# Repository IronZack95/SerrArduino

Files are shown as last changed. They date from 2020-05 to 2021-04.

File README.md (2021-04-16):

# SerrArduino
> Sistema di Automazione per Serra con Arduino

**Author**
- [IronZack95](https://github.com/IronZack95)
 
 ## Instructions:
 1. A_Global_rev7 contiene il codice che ho scritto per Arduino IDE
 2. per vedere lo schema elettrico aprire "Arduino_Serra.fzz" con FRITZING
 3. Cartella "Test" per testare il funzionamento componenti singoli
 4. Board_Schematic contiene lo schema SPice e un pdf per il pinout della boad millefori

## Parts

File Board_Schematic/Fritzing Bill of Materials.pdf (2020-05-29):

29/5/2020 | Fritzing Bill of Materials
file:///C:/Users/Utente/Documents/GitHub/SerrArduino/Board_Schematic/Arduino_Serra_bom.html | 1/3

# Bill of Materials: Arduino_Serra.fzz

C:/Users/Utente/Documents/GitHub/SerrArduino/Arduino_Serra.fzz
venerdì, maggio 29 2020, 17:27:59

# Assembly List

Label | Part Type | Properties
Componente1 | Arduino Uno
| (Rev3) | tipo Arduino UNO (Rev3)

### DHT11

### DHT11 Humitidy and Temperature Sensor

### ENCODER1

### Rotary Encoder with switch (KY-

040)

variant KY-040; part number KY-040

J1 | Basic Servo
LCD1 | LCD screen | tipo Character; pins 16
M1 | DC Motor

### Modulo

Motore | L293D | package THT; variant L293D

### Part1

KY-022

### Infrared Receiver Module

operating voltage 2.7V to 5.5V; variant variant 1; operating current 0.4 ~ 1.5 mA; low level voltage 0.4V; reception distance 18m; high level voltage 4.5V; ambient light filter up to 500LUX; pin spacing 300mil; dimensions 18.5mm x 15mm [0.728in x 0.591in]; editable pin labels false; reception angle ±45º; operating temperature -25°C to 80°C [-13°F to 176°F]; ir receiver 1838; chip label KY-022; package Breakout board; pins 3

R1 | PHOTOCELL | package photocell-kit; variant pth-kit
R2 | Trimmer

### Potentiometer

| | package THT; size Trimmer - 12mm; track Linear; tipo Trimmer Potentiometer;
| | maximum resistance 10kΩ
R3 | 1k Ω Resistor | package THT; tolerance ±5%; bands 4; resistenza 1kΩ; pin spacing 400 mil

R4

### Temperature Sensor (Thermistor)

| | resistance at 25° 10kΩ; package THT; thermistor type NTC; tipo thermistor
R5 | 10k Ω
| Resistor | package THT; tolerance ±5%; bands 4; resistenza 10kΩ; pin spacing 400 mil
R7 | 500 Ω
| Resistor | package THT; tolerance ±5%; bands 4; resistenza 500Ω; pin spacing 400 mil

file:///C:/Users/Utente/Documents/GitHub/SerrArduino/Board_Schematic/Arduino_Serra_bom.html | 2/3
Label | Part Type | Properties
R9 | 500 Ω
Resistor | package THT; tolerance ±5%; bands 4; resistenza 500Ω; pin spacing 400 mil
Relè | KY-019 5V

### Relay Module

package Breakout board; dimensions 27mm x 34mm [1.063in x 1.338in]; maximum ac 10A 250VAC; operating voltage 5V ~ 12V; editable pin labels false; chip label KY-019; variant variant 1; pins 3; pin spacing 300mil; maximum dc 10A 30VDC
RTC Clock | Adafruit
DS3231 | variant variant 2; part number Adafruit #3013
S1 | Toggle Switch | package THT; switching circuit SPDT
S2 | Toggle Switch | package THT; switching circuit SPDT

# Shopping List

Amount | Part Type | Properties

1

### Arduino Uno

(Rev3) | tipo Arduino UNO (Rev3)

1

### DHT11 Humitidy and Temperature Sensor

1

### Rotary Encoder with switch (KY-

040)

variant KY-040; part number KY-040

1 | Basic Servo
1 | LCD screen | tipo Character; pins 16
1 | DC Motor
1 | L293D | package THT; variant L293D

1

KY-022

### Infrared Receiver Module

operating voltage 2.7V to 5.5V; variant variant 1; operating current 0.4 ~ 1.5 mA; low level voltage 0.4V; reception distance 18m; high level voltage 4.5V; ambient light filter up to 500LUX; pin spacing 300mil; dimensions 18.5mm x 15mm [0.728in x 0.591in]; editable pin labels false; reception angle ±45º; operating temperature -25°C to 80°C [-13°F to 176°F]; ir receiver 1838; chip label KY-022; package Breakout board; pins 3

1 | PHOTOCELL | package photocell-kit; variant pth-kit

1

### Trimmer Potentiometer

| | package THT; size Trimmer - 12mm; track Linear; tipo Trimmer Potentiometer; maximum resistance 10kΩ
1 | 1k Ω Resistor | package THT; tolerance ±5%; bands 4; resistenza 1kΩ; pin spacing 400 mil

1

### Temperature Sensor (Thermistor)

| | resistance at 25° 10kΩ; package THT; thermistor type NTC; tipo thermistor

file:///C:/Users/Utente/Documents/GitHub/SerrArduino/Board_Schematic/Arduino_Serra_bom.html | 3/3
Amount | Part Type | Properties
1 | 10k Ω
| Resistor | package THT; tolerance ±5%; bands 4; resistenza 10kΩ; pin spacing 400 mil
2 | 500 Ω
| Resistor | package THT; tolerance ±5%; bands 4; resistenza 500Ω; pin spacing 400 mil
1 | KY-019 5V
| Relay Module | package Breakout board; dimensions 27mm x 34mm [1.063in x 1.338in]; maximum ac
| | 10A 250VAC; operating voltage 5V ~ 12V; editable pin labels false; chip label KY-019;
| | variant variant 1; pins 3; pin spacing 300mil; maximum dc 10A 30VDC
1 | Adafruit
| DS3231 | variant variant 2; part number Adafruit #3013
2 | Toggle Switch | package THT; switching circuit SPDT

Exported with Fritzing 0.8.7- http://fritzing.org

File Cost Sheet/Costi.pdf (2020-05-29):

Foglio1

29/05/20

TABELLA COSTI
Componente | Prezzo | QTA | Prezzo Totale

GBC ELETTRONICA

Fotoresistenza | 1,2 | 2 | 2,4
Mille Fori | 5 | 1 | 5
| 5 | 1 | 5
L293D Integrato | 5,5 | 1 | 5,5
10k ohm Potenziometro | 1,5 | 1 | 1,5
Stagno 60/40 | 8 | 0,25 | 2
| 0,4 | 2 | 0,8
| 0,8 | 1 | 0,8
Alimentatore 220AC/12DC | 7,9 | 1 | 7,9
Connettore Dorato 40PM | 0,8 | 2 | 1,6
Cavo Alimentazione bianco | 1 | 2 | 2
Spina 220V 10A Bianca | 1,5 | 1 | 1,5
Deviatore 2 vie | 1,5 | 1 | 1,5
Ventola 12V | 4,5 | 1 | 4,5

AMAZON

LERWAY Tappetino Riscaldante | 19,9 | 1 | 19,9
IZOKEE 60 Pezzi Morsetti | 9,9 | 0,5 | 4,95
ELEGOO UNO Rev3 | 12,99 | 1 | 12,99
| 54,99 | 1 | 54,99
| 7,99 | 0,2 | 1,598
| 7 | 0,5 | 3,5
| | | SOMMA
| | | 139,928

## SerrArduino

Modulo Step-Down DC\DC

Piattina Red-Black
Zoccolo16 Pin

ELEGOO Starter Kit
Arceli 5pz
Modulo Irreciver 2pz

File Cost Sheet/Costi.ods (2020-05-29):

SerrArduino | 29/05/20
TABELLA COSTI
Componente | Prezzo | QTA | Prezzo Totale
GBC ELETTRONICA
Fotoresistenza | 1,2 | 2 | 2,4
Mille Fori | 5 | 1 | 5
Modulo Step-Down DC\DC | 5 | 1 | 5
L293D Integrato | 5,5 | 1 | 5,5
10k ohm Potenziometro | 1,5 | 1 | 1,5
Stagno 60/40 | 8 | 0,25 | 2
Piattina Red-Black | 0,4 | 2 | 0,8
Zoccolo16 Pin | 0,8 | 1 | 0,8
Alimentatore 220AC/12DC | 7,9 | 1 | 7,9
Connettore Dorato 40PM | 0,8 | 2 | 1,6
Cavo Alimentazione bianco | 1 | 2 | 2
Spina 220V 10A Bianca | 1,5 | 1 | 1,5
Deviatore 2 vie | 1,5 | 1 | 1,5
Ventola 12V | 4,5 | 1 | 4,5
AMAZON
LERWAY Tappetino Riscaldante | 19,9 | 1 | 19,9
IZOKEE 60 Pezzi Morsetti | 9,9 | 0,5 | 4,95
ELEGOO UNO Rev3 | 12,99 | 1 | 12,99
ELEGOO Starter Kit | 54,99 | 1 | 54,99
Arceli 5pz | 7,99 | 0,2 | 1,598
Modulo Irreciver 2pz | 7 | 0,5 | 3,5
 |  |  | SOMMA
 |  |  | 139,928

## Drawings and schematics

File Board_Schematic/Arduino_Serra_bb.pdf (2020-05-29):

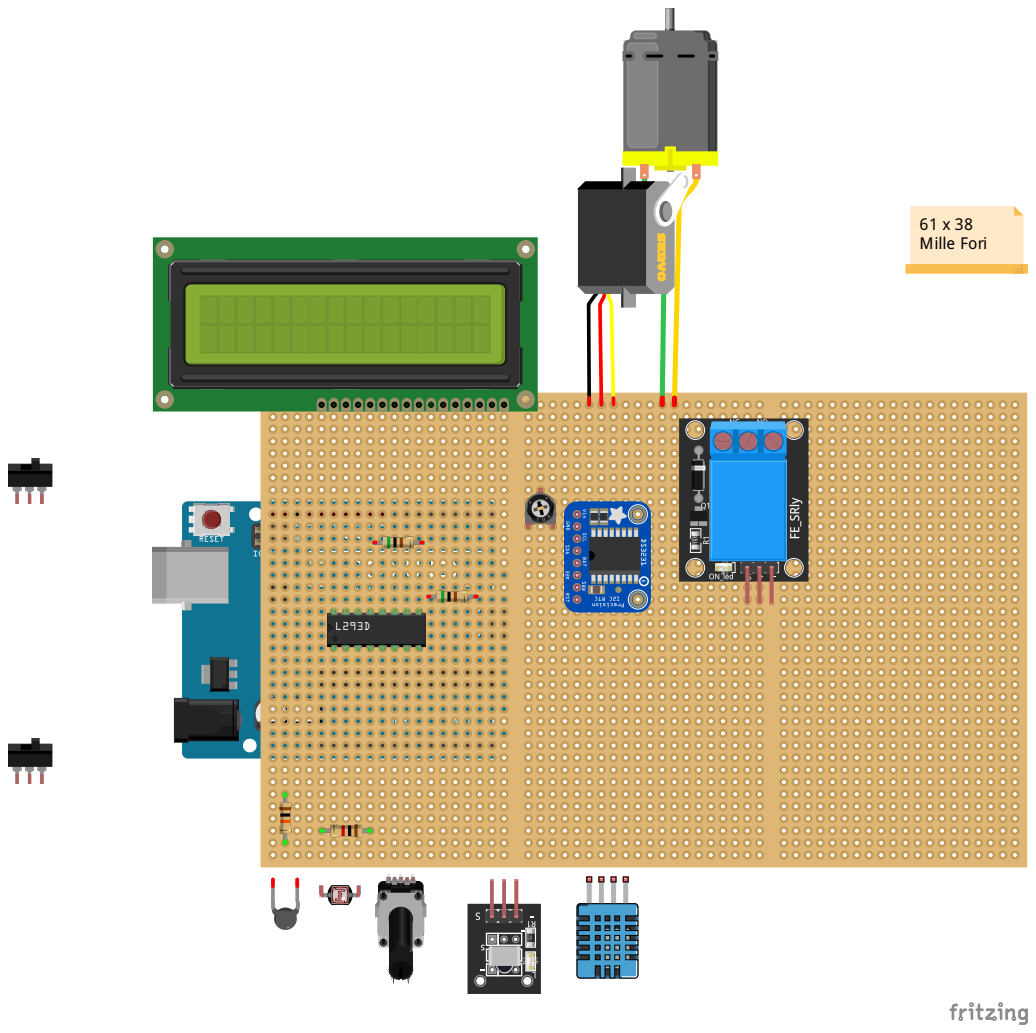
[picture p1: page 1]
61 x 38 Mille Fori

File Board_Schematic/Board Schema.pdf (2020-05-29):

1

2

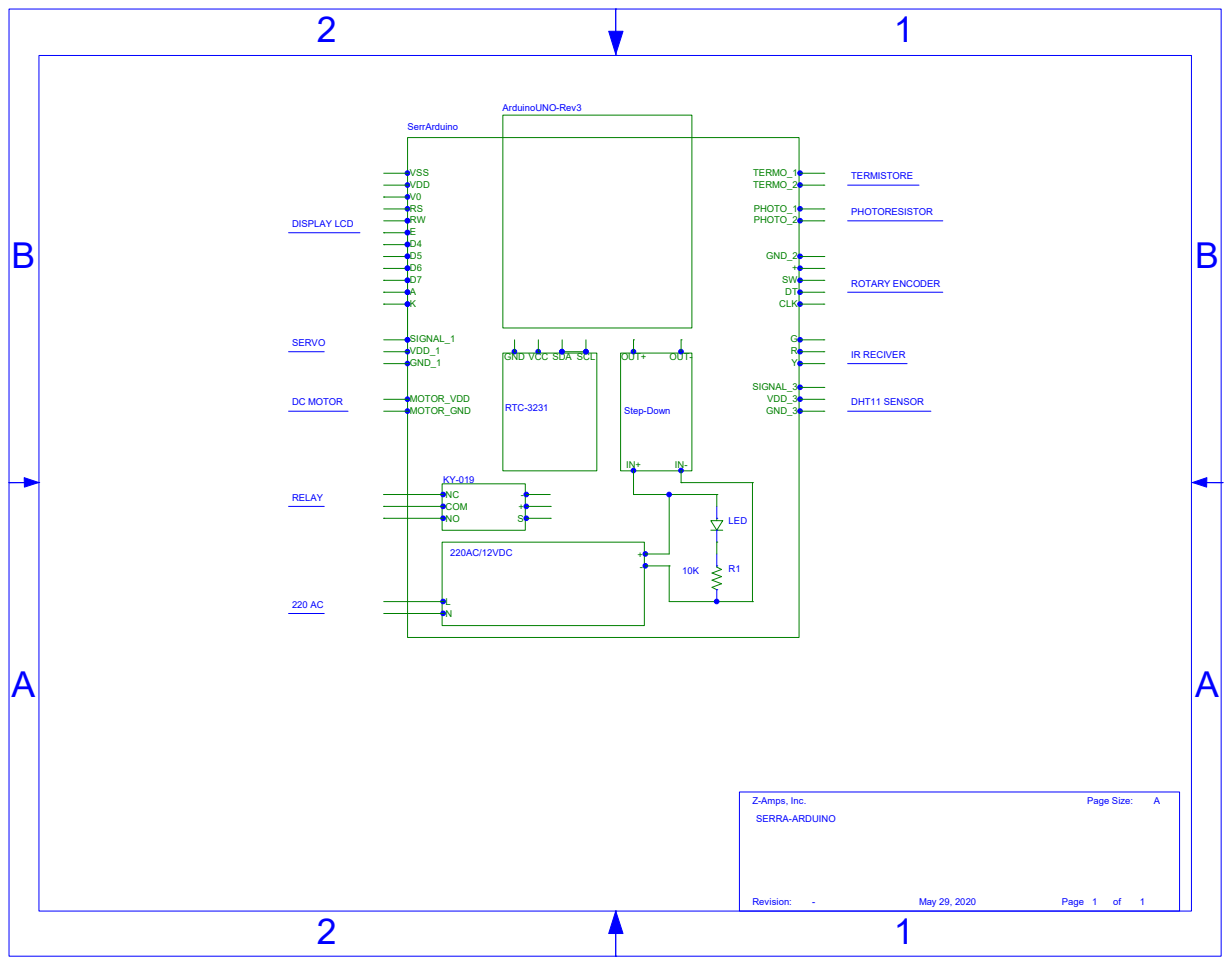
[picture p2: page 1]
COM; 220AC/12VDC; OUT+; OUT-; Step-Down; VSS VDD V0; SIGNAL_1 VDD_1 GND_1; MOTOR_VDD MOTOR_GND; TERMO_1 TERMO_2; PHOTO_1 PHOTO_2; GND_2 + SW DT CLK; SIGNAL_3 VDD_3 GND_3; SerrArduino; LED; ArduinoUNO-Rev3; RTC-3231; Revision:; Page; Z-Amps, Inc.; Page Size:; May 29, 2020; SERVO; DC MOTOR; RELAY; DISPLAY LCD; TERMISTORE; PHOTORESISTOR; IR RECIVER; DHT11 SENSOR; ROTARY ENCODER; SERRA-ARDUINO

GND VCC SDA SCL

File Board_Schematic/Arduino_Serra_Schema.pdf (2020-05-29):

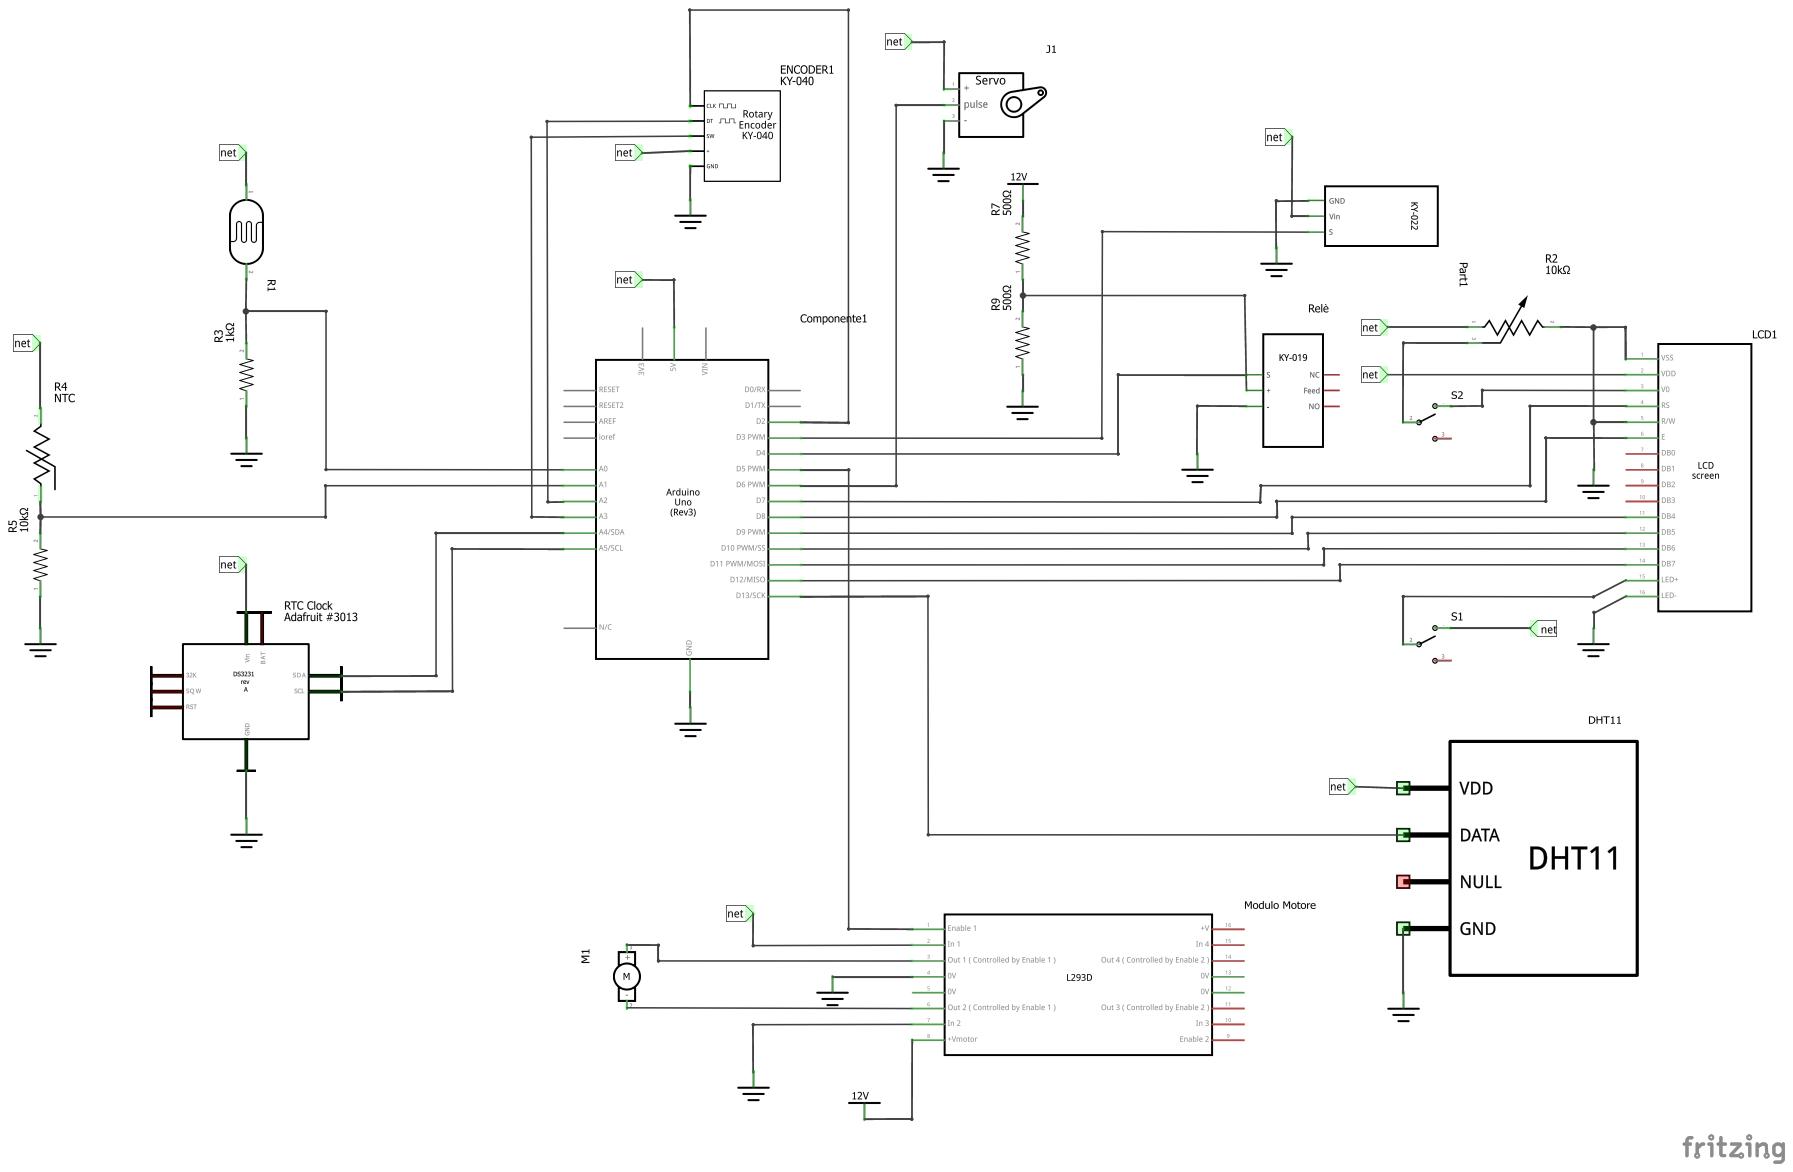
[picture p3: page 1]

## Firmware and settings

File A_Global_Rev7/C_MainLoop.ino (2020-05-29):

// MAIN LOOP

void loop() {

      int err = OK;
      
      //Inizio con i rilevamenti
      //Clock
      RealTimeClock();

      //Rileva Interrupt
      Detect_Interrupt();

      //Rileva Bottone
      Detect_Button();
      
      //Rileva Allarme
      Detect_Allarm();

      //Rileva Telecomando
      //Detect_Reciver();

      if(mod != 0){                     //-----------  ENTRA IN MODALITA' UI

             UI(); 

            // Verifico che sia passato un tot di tempo dall'ultimo interrupt
            UItoAUTOMATIC();
            del = UI_SAMPLING_RATE;             // Sampling Rate
            
            skip = skip + UI_SAMPLING_RATE;
            
            if(skip >= AUTOMATIC_SAMPLING_RATE){
              //Esegue automatismo
              err = Automatic();
              if(err != OK){
                return;
                }
              skip = 0;              
            }
                       
      }else{                                      //-----------  ENTRA IN MODALITA' AUTOMATICA
            //Esegue automatismo
            err = Automatic();
            /*
            if(err != OK){
              return;
              }
            */
            Loop_Serial_div();      // Divisorio  
            del = AUTOMATIC_SAMPLING_RATE;      // Sampling Rate
      }

      // Leggo quello che ho scitto dalla porta Seriale
      Serial_Read();
      
      // ripeto
      //Loop_Serial_div();      // Divisorio
      delay(del);

}

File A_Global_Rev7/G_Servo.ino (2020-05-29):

void ServoPos(int posizione_voluta){
        //goes from 0 degrees to 180 degrees
        //Serial.print("Direzione: ");
        bool direct = true;
        
        if(posizione_voluta > ultima_posizione){
                for( int pos = ultima_posizione; pos <= posizione_voluta ; pos += 1) {         // in steps of 1 degree
                        myservo.write(pos);       // tell servo to go to position in variable 'pos'
                        delay(15);                // waits 15ms for the servo to reach the position
                        posizione = pos;
                        //Serial.print("Posizione Servo : " ); Serial.println(pos);     
                } 
                direct = true;        
                                
        }else if(posizione_voluta < ultima_posizione){
                for ( int pos = ultima_posizione; pos >= posizione_voluta ; pos -= 1) {         // in steps of 1 degree
                        myservo.write(pos);       // tell servo to go to position in variable 'pos'
                        delay(15);                // waits 15ms for the servo to reach the position
                        posizione = pos;
                        //Serial.print("Posizione Servo : " ); Serial.println(pos);     
                }
                direct = false;
        } else{};

        // assestamento servo
        for(int ii = 0; ii < CicliFermo ; ii++){
                        if(direct == true){
                              posizione_voluta = posizione_voluta - Gradi;
                        }else{
                              posizione_voluta = posizione_voluta + Gradi;
                        }
                        direct = !direct;
                        myservo.write(posizione_voluta);
                        delay(15);                // waits 15ms for the servo to reach the position
                        posizione = posizione_voluta;
                }

        
        posizione = posizione_voluta;
        ultima_posizione = posizione_voluta;
        
    
    return;
  }

void ServoLight(){
  
    // comunicazione servo provvisoria
    float posizion = light_percentuale*(MAXSERVO/100);
    if((int)posizion != posizione) {
        ServoPos((int)posizion);
    }
    
    return;
  }


void GestioneIrrigazione(){
  
    Serial.println(F("GESTIONE IRRIGAZIONE"));
    int unixtime =  (int)dt.minute + 60*(int)dt.hour;
    //Serial.println(unixtime);
    int starttimeM =  (int)EEPROM.read(Address_MATNSTRT_M) + 60*(int)EEPROM.read(Address_MATNSTRT_H);
    int stoptimeM = starttimeM + (int)EEPROM.read(Address_DURIRRIG_M) + 60*(int)EEPROM.read(Address_DURIRRIG_H);
    //Serial.println(starttimeM);  Serial.println(stoptimeM);
    
    int starttimeS =  (int)EEPROM.read(Address_SERASTRT_M) + 60*(int)EEPROM.read(Address_SERASTRT_H);
    int stoptimeS = starttimeS + (int)EEPROM.read(Address_DURIRRIG_M) + 60*(int)EEPROM.read(Address_DURIRRIG_H);
    //Serial.println(starttimeS);  Serial.println(stoptimeS);
  
      if(IrrigMod != 0){ 
          IrrigMod = ModalitaIrrigazione(unixtime, starttimeM, stoptimeM, starttimeS, stoptimeS);
          Serial.print("Modalità: ");  Serial.println(IrrigMod);
      }
      if(IrrigMod == 1){
          IrrigazioneMS( unixtime, starttimeM, stoptimeM, starttimeS, stoptimeS);    
      }else if(IrrigMod == 2){
          IrrigazioneFix(unixtime);
      }
      
  return;
  }


int ModalitaIrrigazione(int unixtime,int starttimeM,int stoptimeM,int starttimeS,int stoptimeS){

    if(unixtime <= UNIXDAY/2){     // il mezzogiorno divide mattina e sera
        // Gestione Mattina
        if(unixtime < starttimeM  ||  unixtime > stoptimeM){
            IrrigMod = 2;
          }else if(unixtime >= starttimeM && unixtime <= stoptimeM){
            IrrigMod = 1;
          }
     }else{
        // Gestione Sera
        if(unixtime < starttimeS ||  unixtime > stoptimeS){
            IrrigMod = 2;
          }else if(unixtime >= starttimeS && unixtime <= stoptimeS){
            IrrigMod = 1;
          }
     }
      return IrrigMod;
  }
 
void IrrigazioneMS(int unixtime,int starttimeM,int stoptimeM,int starttimeS,int stoptimeS){
  
     if(unixtime <= UNIXDAY/2){     // il mezzogiorno divide mattina e sera
        // Gestione Mattina
            if(unixtime >= starttimeM && unixtime <= stoptimeM){
              InterruttoreServo(true);
              last_irrig_fix = unixtime;
            }else{
              InterruttoreServo(false);
              }
     }else{
        // Gestione Sera
            if(unixtime >= starttimeS && unixtime <= stoptimeS){
              InterruttoreServo(true);
              last_irrig_fix = unixtime;
            }else{
              InterruttoreServo(false);
              }
     }
    return;
    }

void IrrigazioneFix(int unixtime){
    
    if(irrigazione == true  && unixtime - last_irrig_fix >= (int)EEPROM.read(Address_DURIRGZFIX)){
          Serial.println(F("Irrigazione fissa: "));
          InterruttoreServo(false);
          last_irrig_fix = unixtime;
      }
      if(irrigazione == false  && unixtime - last_irrig_fix >= (int)EEPROM.read(Address_PERIRGZFIX)){
          Serial.println(F("Irrigazione fissa: "));
          InterruttoreServo(true);
          last_irrig_fix = unixtime;
      }
      
  return;
  }

void InterruttoreServo(bool state){
    if(state == true){
      ServoPos((int)MAXSERVO);    // Apro
      irrigazione = true;         //aggiorno lo stato
      Serial.println(F("Apro")); 
    }else{
      ServoPos((int)MINSERVO);    // Chiudo
      irrigazione = false;        //aggiorno lo stato
      Serial.println(F("Chiudo")); 
    }
    
  return;
  }

void StopServo(){
      if(IrrigMod != 0){
        InterruttoreServo(false);
        IrrigMod = 0;
      }else{
         IrrigMod = 1;
      }
  return;
  }

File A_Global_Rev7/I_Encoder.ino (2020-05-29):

// Interrupt routine runs if CLK goes from HIGH to LOW
void isr ()  {
    delay(4);  // delay for Debouncing
    if (digitalRead(PinCLK))
      rotationdirection= digitalRead(PinDT);
    else
      rotationdirection= !digitalRead(PinDT);
      

    // Salva time dell'ultimo evento
    Last_Unix_time = dt.unixtime;
    TurnDetected = true;
    Serial.println(F("Rotary Interrupt"));
  }

void Detect_Interrupt(){
     // Runs if rotation was detected
      if(TurnDetected){
        PrevPosition = RotaryPosition; // Save previous position in variable
        if (rotationdirection) {
          RotaryPosition=RotaryPosition-1;} // decrase Position by 1
        else {
          RotaryPosition=RotaryPosition+1;} // increase Position by 1
        
        // Gestione Rotary  
        Gestione_Rotary();

        
        Serial.println();
        Serial.print(F("RotaryPosition: ")); Serial.println(RotaryPosition);
        Serial.print(F("MAXPAGE: ")); Serial.println(MAXPAGE-1); Serial.print(F("modalità: ")); Serial.println(mod);
        Serial.println();
        
        TurnDetected = false;  // do NOT repeat IF loop until new rotation detected
      }
      return;
  }

void Gestione_Rotary(){
    
    //Gestione Rotary
    if(mod == 0 || mod == 1){               // modalità MENU
      if(RotaryPosition > MAXPAGE-1){
          RotaryPosition = 0;
      }else if(RotaryPosition < 0){
          RotaryPosition = MAXPAGE-1;
      }
      // Gestione pagina
      page = RotaryPosition;
      mod = 1;
    }
    
    if(mod == 2){                
      // modalità MODIFICA
      if(RotaryPosition > MAXVAR){
        RotaryPosition = 0;
      }else if(RotaryPosition < 0){
          RotaryPosition = MAXVAR;
      }
      
      //Gestione pagina
      switch(RotaryPosition){
                case 0: case 1:                 page = 0; break;
                case 2:                         page = 1; break;
                case 3: case 4:                 page = 2; break;
                case 5:                         page = 3; break;
                case 6:                         page = 4; break;
                case 7: case 8: case 9: case 10: page = 5; break;
                case 11: case 12:               page = 6; break;
                case 13:                        page = 7; break;
                case 14:                        page = 8; break;
                default:
                  break;
        }
    }

    if(mod == 3){
           int_table[Sel] = RotaryPosition;
        }
    
    return;
    }

void Detect_Button(){
      if (!(digitalRead(PinSW))){   // check if button is pressed
        if(Button == false){          // check se l'evento del bottone è già avvenuto
           Button = true;
           Serial.println(F("Button Interrupt"));
           //Gestione Bottone
           Gestione_Bottone();
           // Salva time dell'ultimo evento
           Last_Unix_time = dt.unixtime;                  // scateno simil interrupt
        }
      }else{
            Button = false;
      }
      return;
  }

void Gestione_Bottone(){
    //if(Button == true){
    
          if(mod == 0){       // entro in modalità  MENU
            Serial.println(F("MODALITA MENU'"));
            mod = 1;
            Sel = -1;
            page = 0;
            RotaryPosition=0;          
          }

          //Gestione Buttone
          if(mod == 3){       // Confermo cambiamento
            Serial.println(F("MODIFICA EFFETTUATA"));
            RAM_to_EEPROM_Update();
            mod = 0;
            Sel = -1;      
          }
          
          if(mod == 2){       // entro in modalità  selezione
            Serial.println(F("MODALITA SELEZIONE"));
            mod = 3;
            Sel = RotaryPosition;
            RotaryPosition = int_table[Sel];
          }

          if(mod == 1 && page == MAXPAGE-2){       // entro in modalità  Modifica
            Serial.println(F("MODALITA MODIFICA"));
            mod = 2;
            page = 0;
            Sel = -1;
            RotaryPosition=0;
          }

          if(mod == 1 && page == MAXPAGE-1){       // esco dal menu
            Serial.println(F("USCITA"));
            mod = 0;
            Sel = -1;
          }
           
      //}
    return;
  }

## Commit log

2020-05-15 versione Encoder
2020-05-15 Aggiungo file FRITZIG
    schema elettrico
    [Arduino_Serra.fzz]
2020-05-16 Schema fritzig
    [Arduino_Serra.fzz]
2020-05-23 ho modificato lo schema e il codice principale adattato alla nuova ventola
    [Arduino_Serra.fzz]
2020-05-26 Ulteriori update
    lighti pin, sensore tempreatura analogico
    e uscita dal display
2020-05-28 Prototipo funzionante
    Questa versione è implementata sulla millefori in maniera definitiva
    [Arduino_Serra.fzz]
2020-05-29 Aggiungo schema della board
    [SerrArduino_Schematic.sch]
2020-05-29 Aggiungo relè
    ho aggiunto al codice il relè
2020-05-29 modifiche varie
    [Arduino_Serra.fzz, SerrArduino_Schematic.sch]
2020-05-29 Stima Costi
    [Arduino_Serra.fzz, Costi.ods]
2020-05-29 ultime cose
    [Arduino_Serra.fzz, Costi.ods, SerrArduino_Schematic.sch]
